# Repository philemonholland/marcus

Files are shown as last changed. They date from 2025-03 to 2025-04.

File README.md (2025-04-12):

# Projet Animatronique : Marcus

Ce dépôt contient le code et la structure d’architecture pour un système d’animatronique capable de détecter des visages, reconnaître des émotions, parler et bouger la tête via des servomoteurs. L’objectif est de permettre à *Marcus* de réagir en temps réel aux personnes qui l’entourent (détection du regard, conversation audio, expressions faciales, etc.).

---

<!-- HTML image Marcus (resized) -->
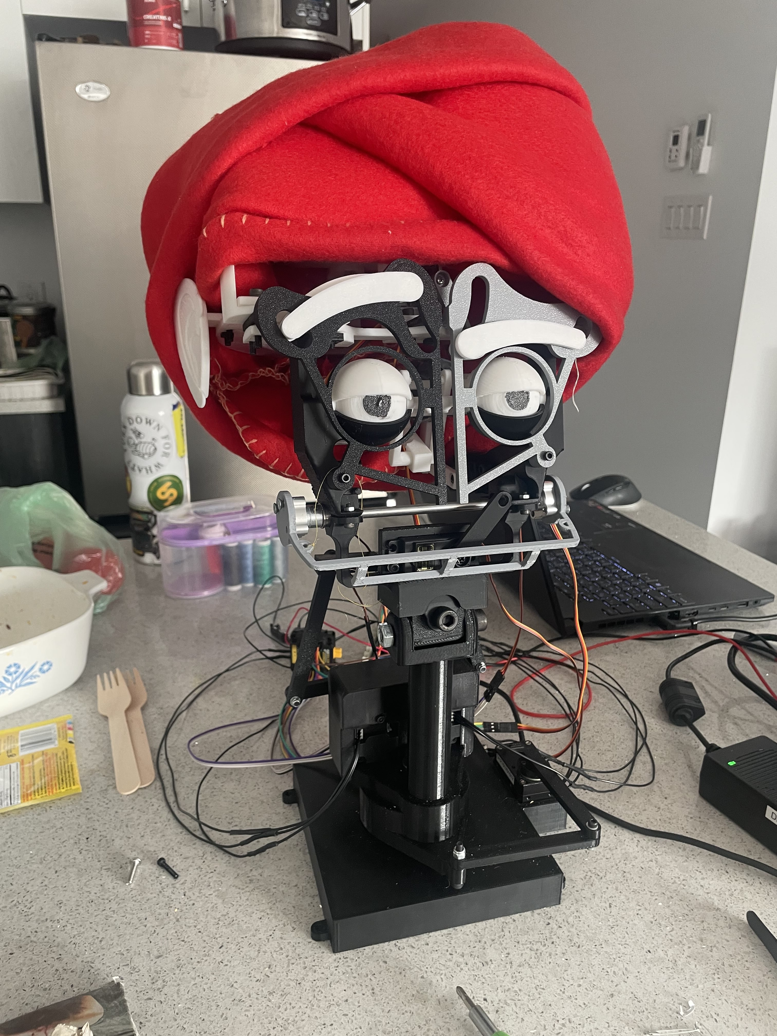
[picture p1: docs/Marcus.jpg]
Marcus illustration


<!-- HTML image Setup (resized) -->
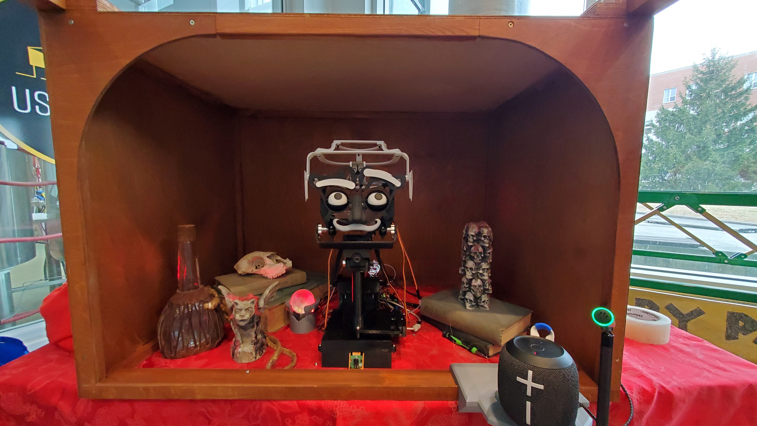
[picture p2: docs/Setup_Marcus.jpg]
Marcus illustration


## Aperçu du fonctionnement

Le diagramme ci-dessous illustre le flux de Communication/Fonctionnement entre les différents composants :

- **Raspberry Pi**  
  *Caméra + Reconnaissance faciale + Reconnaissance d'émotion*  
  Envoi de la position `(x,y,z)` et des émotions détectées via MQTT au PC

- **PC central**  
  - Fait office de **Broker MQTT** 
  - Utilise **Whisper** (STT) pour la reconnaissance vocale  
  - Fait des requêtes au **LLM externe** (OpenAI) via une API REST (avec le contexte : texte + émotion)  
  - Renvoie une réponse texte
  - Gère la **synthèse vocale (TTS)** pour parler via un haut-parleur

- **Arduino OpenRB-150** (contrôle des servos)  
  - Reçoit des commandes UART (*REGARDE, SURPRIS, NON IMPRESSIONER, etc.*)  
  - Envoie son statut (*ready*) au départ  
  - Contrôle effectif des mouvements de la tête

- **Arduino MEGA** (contrôle boule de cristal)  
  - Reçoit des commandes UART (*ALLUME et ÉTEINT*)  
  - Envoie son statut (*ready*) au départ  
  - Contrôle effectif des lumières de la boule de cristal

---

## 📄 License

### Général

Ce projet est distribué sous la licence [MIT](LICENSE) pour tout le code source, les scripts, et les fichiers STL que nous avons créés.  
Veuillez noter que certaines bibliothèques externes utilisées dans ce projet peuvent être soumises à des licences différentes. Il est de votre responsabilité de consulter et de respecter les conditions de licence de ces dépendances.

### 🗣️ Text-to-Speech (TTS)

Ce projet utilise [edge-tts](https://github.com/rany2/edge-tts) pour générer de la parole via le moteur TTS de Microsoft Edge.  
Consultez leur [répertoire GitHub](https://github.com/rany2/edge-tts) pour plus d’informations sur leur licence et leur politique d'utilisation.

### fer2013 : Base de données d'expressions faciales utilisée pour entraîner notre modèle de reconnaissance d'émotion.  
  Source : [Kaggle - FER-2013](https://www.kaggle.com/datasets/msambare/fer2013)  
  Utilisée uniquement à des fins de recherche et d'expérimentation.

### Haar Cascade 
  Utilisé pour la détection de visages. Fichier `haarcascade_frontalface_default.xml` fourni par [OpenCV](https://github.com/opencv/opencv/tree/master/data/haarcascades) sous licence Apache 2.0.

## Structure générale

```bash
marcus/
├── docs/
│   └── ... (Documentation, schémas, etc.)
├── Code/
│   ├── Com/                      (Fonctions de communication MQTT et UART en python)
│   │   └── test_MQTT                             (Code test MQTT entre PC et PI)
│   │   └── test_MQTT_will.py                     (Code test MQTT entre PC et PI avec départ Mosquitto auto)
│   │   └── Test.py                               (Code test pour envoie de commande manuel au OpenRB-150)
│   │   └── dyn_test.py                           (Code test pour envoie de commande manuel spécialisé pour le cou et dynamixel)
│   │   └── Venv_setup.bat                        (Executable pour installer un environnement virtuel avec les requirements automatiquement)
│   │
│   ├── LLM/
│   │   └── marcus_mqtt.py                        (Code principal avec integration complète)
│   │   └── directttsb.py                         (Code modifier pour donner emotion a tts)
│   │   └── whisper_combat.py                     (Code pour transformer les paroles en txt)
│   │   └── Mega.cpp                              (Code pour controler les lumières de la boule de cristal)
│   │
│   ├── Servo/                    (Dossier platformio : Contient le code l'arduino OpenRB-150)
│   │   ├── src/main.cpp                          (Code principal de l'arduino)
│   │   ├── test/Demo.cpp                         (Demo de foncitonnement des moteurs dynamixel)
│   │   └── test/Scan.cpp                         (Code de détection des ID moteurs dynamixel)
│   │   └── test/main_backup.cpp                  (Code main fourni au départ peu modifier)
│   │   └── README                                (Quelque explication du fonctionnement de OpenRB-150)
│   │
│   └── Pi/
│       ├── FaceRecognition.py    (Détection visage, émotion et envoie info MQTT)
│       ├── EmotionRecognitionTraining.py         (Entrainnement d'un modèle IA avec la banque de donné FER2013)
│       ├── fer2013.zip                           (Banque de données FER2013 voir site officiel pour license)
│       ├── haarcascade_frontalface_default.xml   (Modèle IA pour détection de visage voir site officiel pour license)
│       ├── emotion_recognition_model.h5          (Modèle IA entrainé utiliser avec FaceRecognition)
│       ├── 60_model.h5                           (Alternative de modèle IA)
│       └── setup_venv.sh                         (Executable pour installer un environnement virtuel avec les requirements automatiquement)
│
├── STL                           (Dernier fichier stl des pièces imprimer)
│
└── README.md                     (Vous êtes ici)

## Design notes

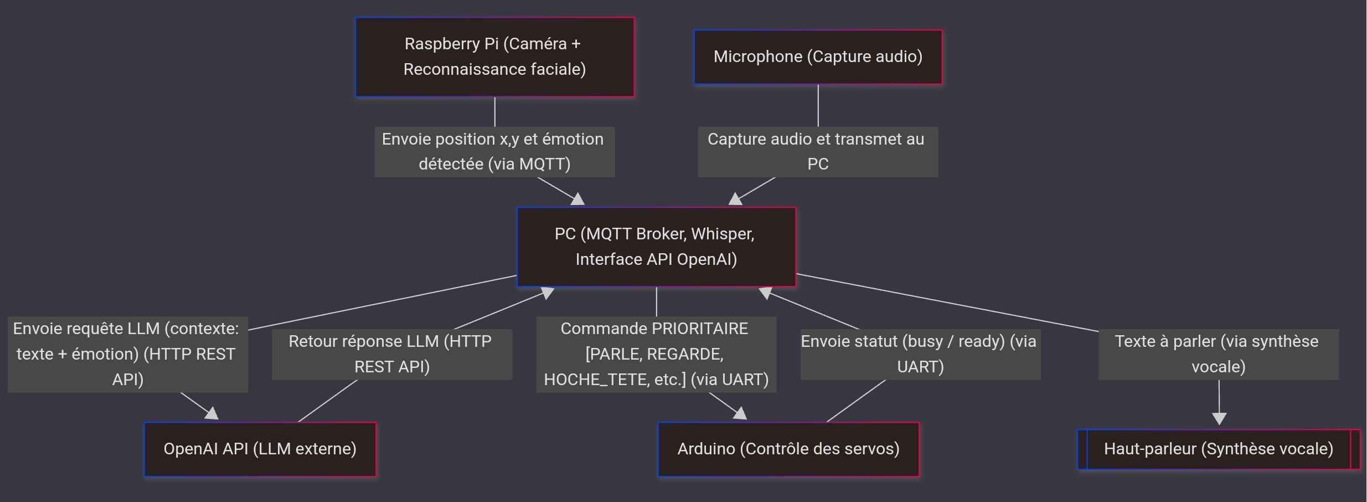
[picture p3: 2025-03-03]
docs/schema_proj.jpg

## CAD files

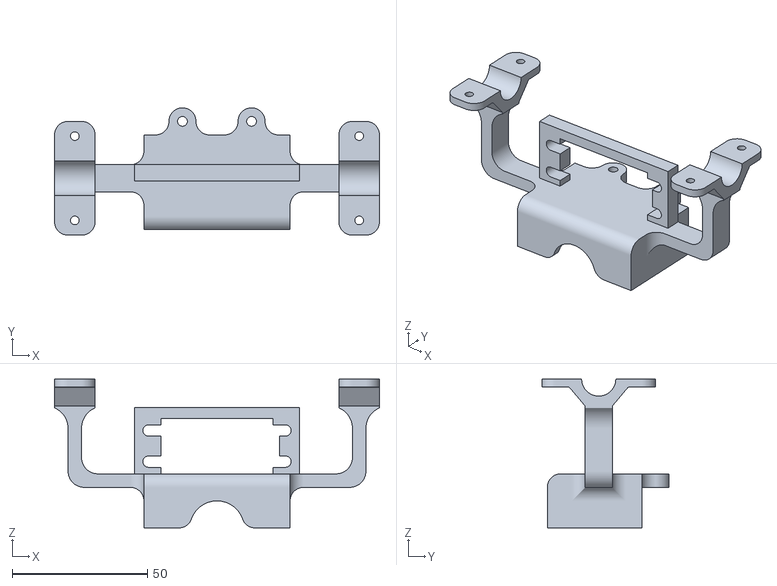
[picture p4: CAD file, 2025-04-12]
STL/Assembly_général/Assembly 1 - Part 1 (26).stl
120.0 x 47.0 x 55.0

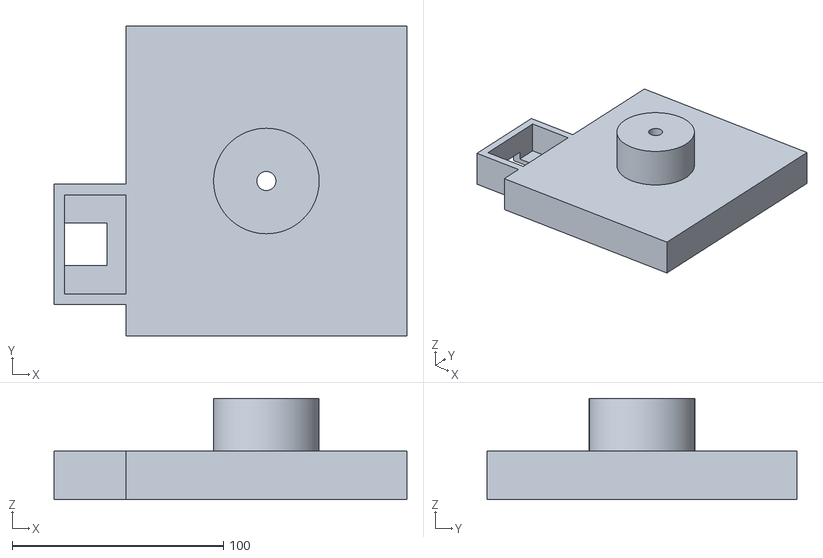
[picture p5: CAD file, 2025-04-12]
STL/Assembly_général/Assembly 1 - Part 1 (28).stl
167.2 x 146.9 x 48.0

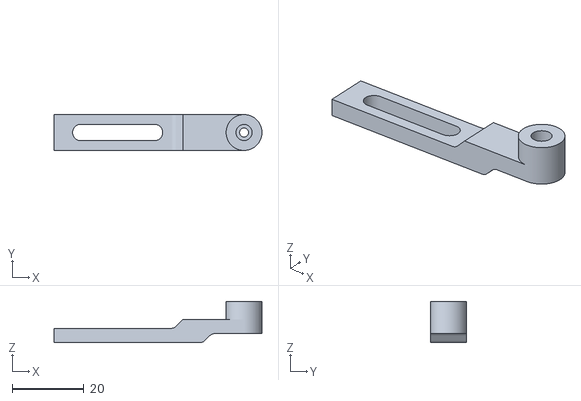
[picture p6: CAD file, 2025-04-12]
STL/Assembly_général/Assembly 1 - Part 1 (12).stl
58.0 x 10.0 x 11.5

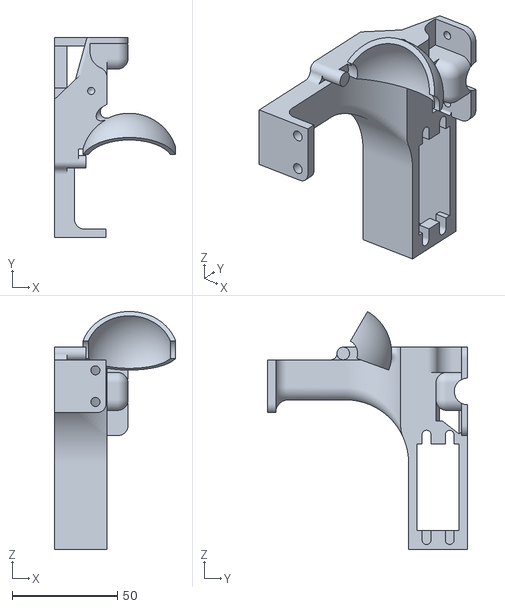
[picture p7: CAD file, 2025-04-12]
STL/Assembly_général/Assembly 1 - Part 1 (18).stl
57.6 x 95.0 x 112.9

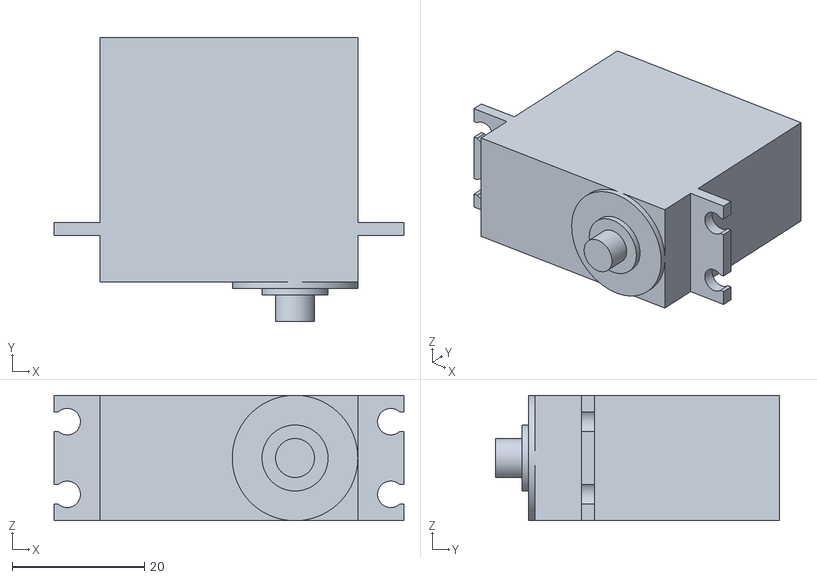
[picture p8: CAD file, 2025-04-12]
STL/Assembly_général/Assembly 1 - Part 1.stl
53.0 x 43.0 x 19.0

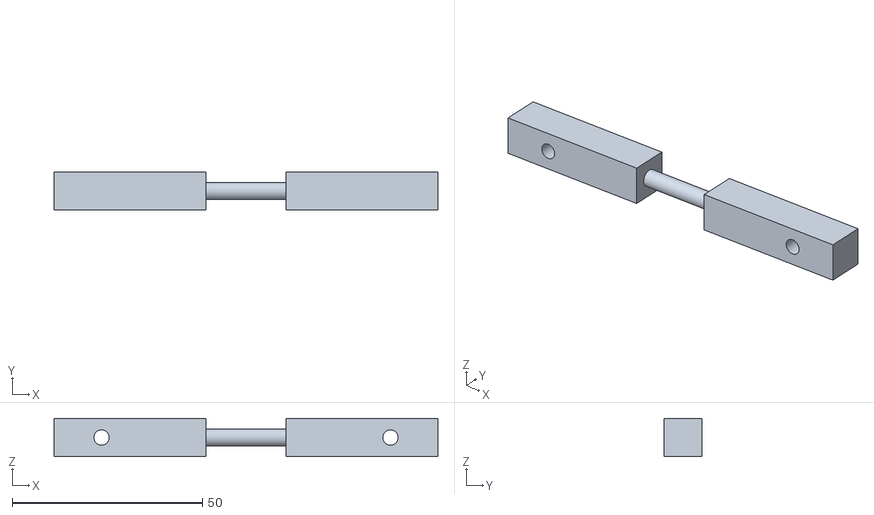
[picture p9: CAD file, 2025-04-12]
STL/Assembly_général/Assembly 1 - Part 4.stl
101.0 x 10.0 x 10.0

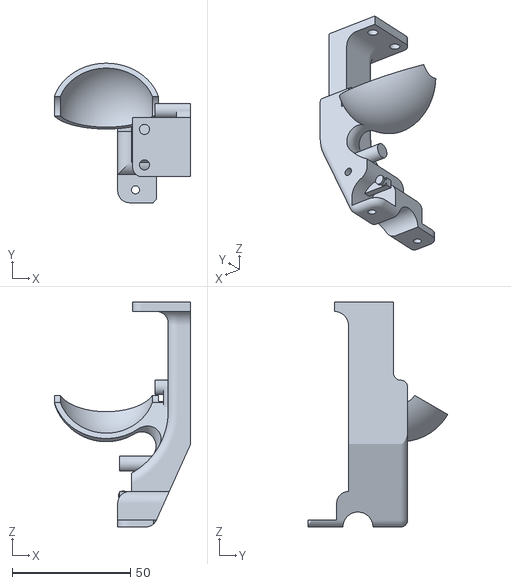
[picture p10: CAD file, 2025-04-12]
STL/Assembly_général/Assembly 1 - Part 1 (19).stl
57.6 x 58.9 x 95.0

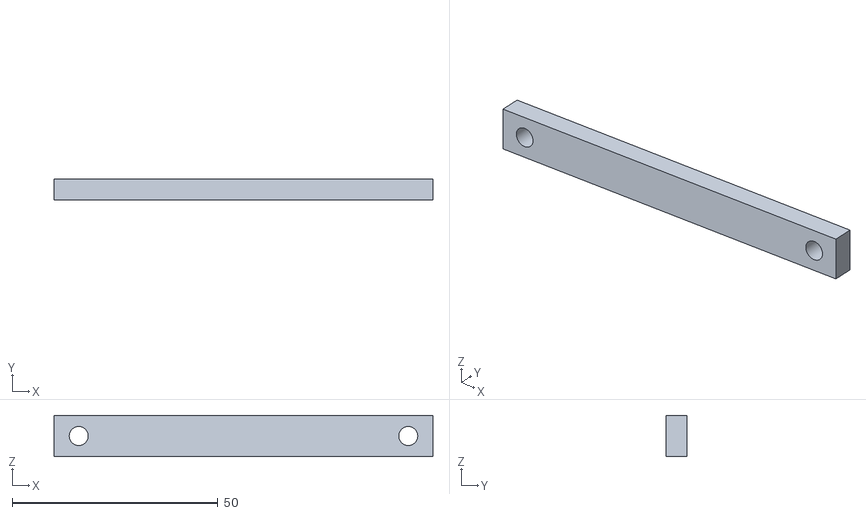
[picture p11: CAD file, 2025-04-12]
STL/Assembly_général/Assembly 1 - Part 1 (11).stl
92.0 x 5.00 x 10.0

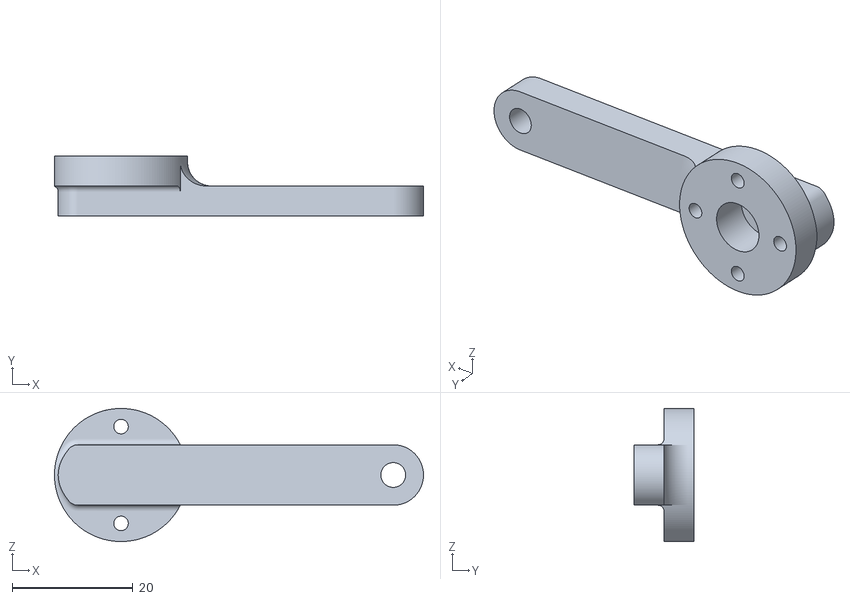
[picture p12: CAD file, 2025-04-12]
STL/Assembly_général/Assembly 1 - Part 1 (10).stl
61.0 x 10.0 x 22.0

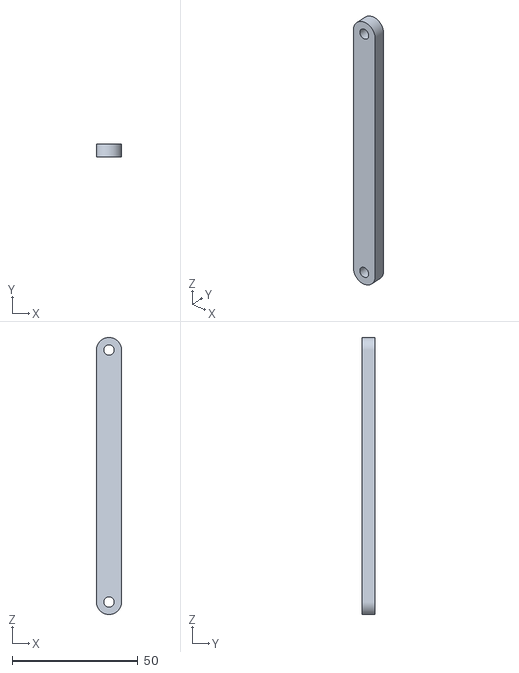
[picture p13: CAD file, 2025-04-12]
STL/Assembly_général/Assembly 1 - Part 2.stl
10.0 x 5.00 x 110.0

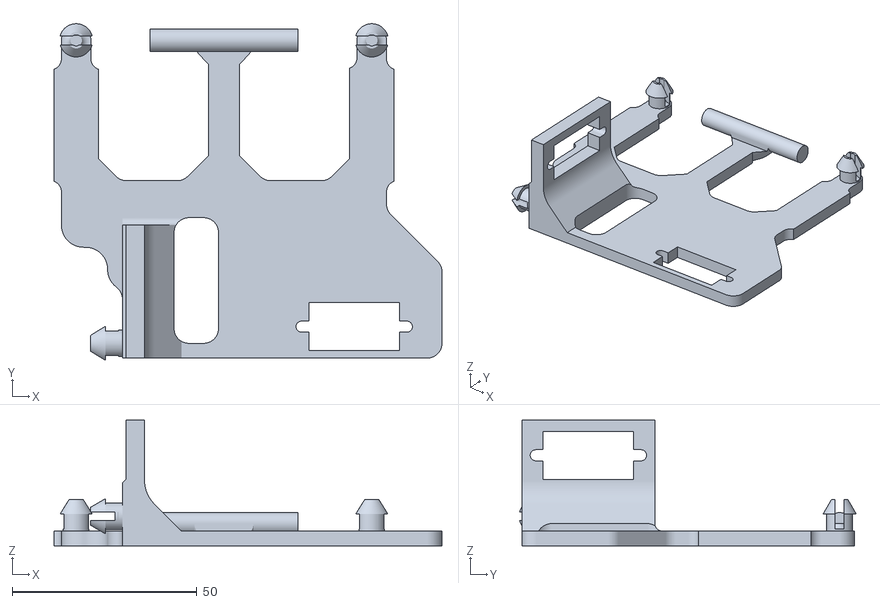
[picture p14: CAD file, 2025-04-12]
STL/Assembly_général/Assembly 1 - Part 1 (17).stl
105.0 x 91.1 x 34.0

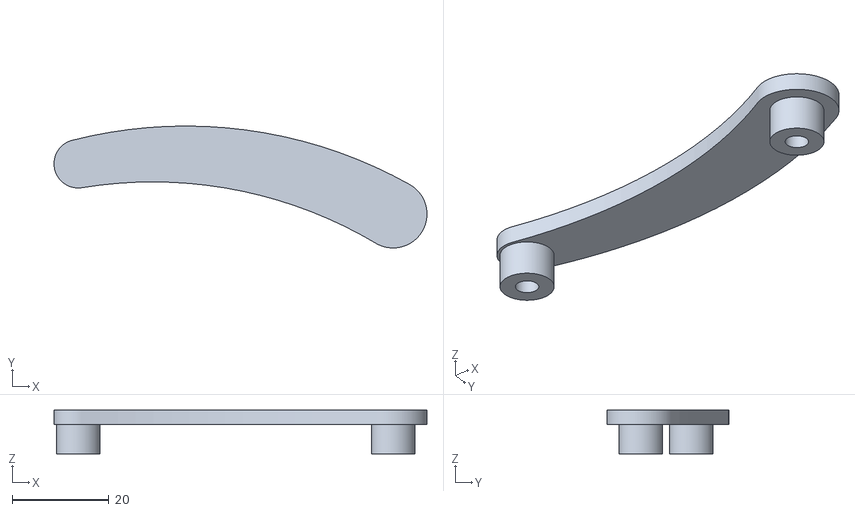
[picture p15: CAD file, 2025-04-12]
STL/Assembly_général/Assembly 1 - Part 1 (22).stl
77.0 x 25.2 x 9.00

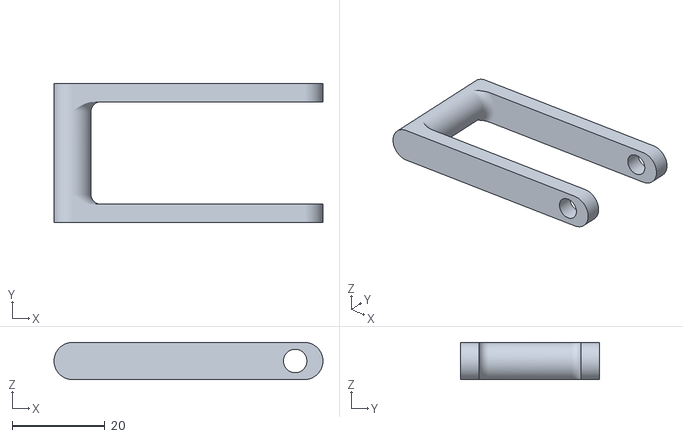
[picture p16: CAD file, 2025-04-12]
STL/Assembly_général/Assembly 1 - Part 1 (16).stl
58.0 x 30.0 x 8.00

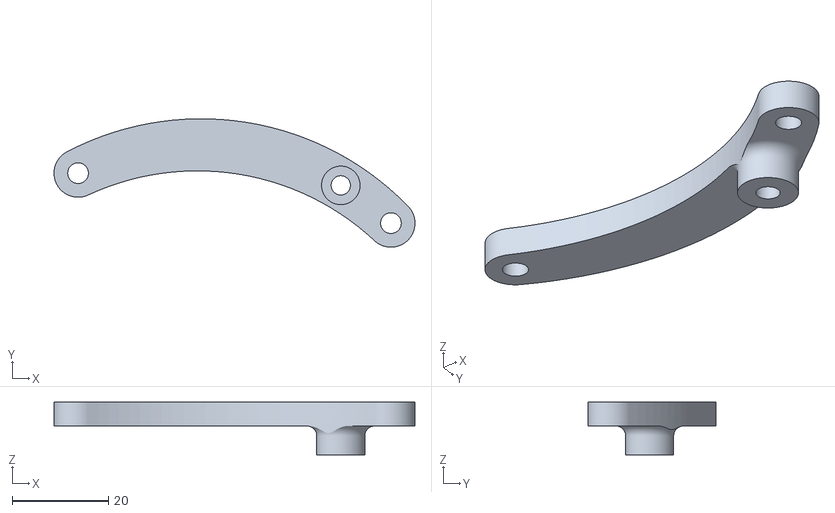
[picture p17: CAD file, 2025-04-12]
STL/Assembly_général/Assembly 1 - Part 1 (25).stl
75.0 x 26.7 x 11.0

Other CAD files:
STL/Assembly_général/Assembly 1 - Part 1 (14).stl
STL/Assembly_général/Assembly 1 - Part 1 (23).stl
STL/Assembly_général/Assembly 1 - Part 1 (20).stl
STL/Assembly_général/Assembly 1 - Part 1 (21).stl
STL/Assembly_général/Assembly 1 - Part 1 (1).stl
STL/Assembly_général/Assembly 1 - Part 1 (13).stl
STL/Assembly_général/Assembly 1 - Part 1 (15).stl
STL/Assembly_général/Assembly 1 - Part 1 (2).stl
STL/Assembly_général/Assembly 1 - Part 1 (24).stl
STL/Assembly_général/Assembly 1 - Part 1 (27).stl
STL/Assembly_général/Assembly 1 - Part 1 (3).stl
STL/Assembly_général/Assembly 1 - Part 1 (4).stl
STL/Assembly_général/Assembly 1 - Part 1 (5).stl
STL/Assembly_général/Assembly 1 - Part 1 (6).stl
STL/Assembly_général/Assembly 1 - Part 1 (7).stl
STL/Assembly_général/Assembly 1 - Part 1 (8).stl
STL/Assembly_général/Assembly 1 - Part 1 (9).stl
STL/Assembly_général/Assembly 1 - Part 2 (1).stl
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

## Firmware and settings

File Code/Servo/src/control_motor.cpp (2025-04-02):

#include <Arduino.h>
#include <Dynamixel2Arduino.h>
#include <Servo.h>
#include <stdio.h>
#include <string.h>

#define PROTOCOL_VERSION 2.0
#define DXL_MIN_ANGLE 0
#define DXL_MAX_ANGLE 4095
#define DXL_MOVING_STATUS_THRESHOLD 20

class Motor {
public:
    virtual void set_angle_degrees(float degrees) = 0;
    virtual int get_angle() = 0;
};

class ServoMotor : public Motor {
public:
    ServoMotor(const char* name, int pin) : name(name), pin(pin), initial_angle(0), angle(0) {
        servo.attach(pin);
        set_angle_degrees(initial_angle);
    }
    void set_angle_degrees(float degrees) override {
        angle = constrain(degrees, 0, 180);
        servo.write(map(angle, 0, 180, 0, 180));
    }
    int get_angle() override {
        return angle;
    }
private:
    const char* name;
    int pin;
    float initial_angle;
    float angle;
    Servo servo;
};

class DynamixelMotor : public Motor {
public:
    DynamixelMotor(const char* name, uint8_t id, uint8_t dir_pin, uint8_t baudrate) 
        : name(name), id(id), initial_angle(2048), angle(2048), driver(Serial1, dir_pin) {
        driver.begin(baudrate);
        set_angle_degrees(initial_angle);
    }
    void set_angle_degrees(float degrees) override {
        int new_angle = map(degrees, 0, 360, DXL_MIN_ANGLE, DXL_MAX_ANGLE);
        set_angle(new_angle);
    }
    int get_angle() override {
        return driver.readControlTableItem(ControlTableItem::PRESENT_POSITION, id);
    }
private:
    void set_angle(int new_angle) {
        angle = constrain(new_angle, DXL_MIN_ANGLE, DXL_MAX_ANGLE);
        driver.writeControlTableItem(ControlTableItem::GOAL_POSITION, id, angle);
    }
    const char* name;
    uint8_t id;
    int initial_angle;
    int angle;
    Dynamixel2Arduino driver;
};

class MotorController {
public:
    void add_motor(Motor* motor, const char* name) {
        if (motor_count < MAX_MOTORS) {
            motors[motor_count].motor = motor;
            motors[motor_count].name = name;
            motor_count++;
        }
    }

    void set_motor(const char* name, float degrees) {
        Motor* motor = find_motor(name);
        if (motor) {
            motor->set_angle_degrees(degrees);
        }
    }

    int get_motor(const char* name) {
        Motor* motor = find_motor(name);
        return motor ? motor->get_angle() : -1;
    }
    
    void reset_all() {
        for (int i = 0; i < motor_count; i++) {
            motors[i].motor->set_angle_degrees(0);
        }
    }

    void set_mirrored_motors(const char* motor1_name, const char* motor2_name, float degrees) {
        Motor* motor1 = find_motor(motor1_name);
        Motor* motor2 = find_motor(motor2_name);
        
        if (motor1 && motor2) {
            float angles = compute_motor_angles(degrees);
            motor1->set_angle_degrees(angles);
            motor2->set_angle_degrees(180 - angles);
        }
    }

    float compute_motor_angle(float pourcentage, const std::string& side = "right") {

        float angle_min = 95.669;
        float angle_max = 151.228931;
        
        float angle_moteur = map(pourcentage, 0, 100, angle_min, angle_max);
    
        if (side == "left") {
            angle_moteur = angle_max - (angle_moteur - angle_min);
        }
    
        return angle_moteur;
    }
    

    void base_motor(const char* motor_name, float degrees) {
        Motor* motor = find_motor(motor_name);
        
        if (motor) {
            float angles = map(degrees, 45, 135, 45, 135);  // changer les valeurs de 45 et 135 pour avoir les angles limites du moteur et leur proportionalité de mouvement tête
            motor->set_angle_degrees(angles);
        }
    }

    float* compute_motor_angles(float final_angle) {

        float norm_value = map(final_angle, 60, 135, 0, 1);  // changer les valeurs de 60 et 135 pour avoir l'angle le plus bas de la tête et l'angle le plus haut
    
        float motor_angle = map(norm_value, 0, 1, 25, 180); // changer les valeurs de 25 et 180 pour avoir l'angle limite des moteurs
    
        float angles = motor_angle;
    
        return angles;
    }


private:
    static constexpr int MAX_MOTORS = 10;
    struct MotorEntry {
        const char* name;
        Motor* motor;
    } motors[MAX_MOTORS];
    int motor_count = 0;
    
    Motor* find_motor(const char* name) {
        for (int i = 0; i < motor_count; i++) {
            if (strcmp(motors[i].name, name) == 0) {
                return motors[i].motor;
            }
        }
        return nullptr;
    }
};

ServoMotor xServo("xServo", 2);
ServoMotor yServo("yServo", 3);
DynamixelMotor xDyn("xDyn", 1, 2, 57600);
DynamixelMotor yDyn("yDyn", 2, 2, 57600);
MotorController controller;

void setup() {
    controller.add_motor(&xServo, "xServo");
    controller.add_motor(&yServo, "yServo");
    controller.add_motor(&xDyn, "xDyn");
    controller.add_motor(&yDyn, "yDyn");
}

void loop() {
    if(controller.get_motor("xServo") == 0 && controller.get_motor("yServo") == 0) {
        controller.set_motor("xServo", 180);
        controller.set_motor("yServo", 180);
    } 
    else if(controller.get_motor("xServo") == 180 && controller.get_motor("yServo") == 180) {
        controller.set_motor("xServo", 0);
        controller.set_motor("yServo", 0);
    }
}

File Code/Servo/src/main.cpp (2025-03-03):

#include <Dynamixel2Arduino.h>
#include <Servo.h>



// Setup environnement dynamixel

#if defined(ARDUINO_OpenRB)  
  #define DXL_SERIAL Serial1 // OpenRB-150 uses Serial1 for Dynamixel
  #define PC_SERIAL Serial // USB Serial for PC communication

  const int DXL_DIR_PIN = -1;
  const float DXL_PROTOCOL_VERSION = 2.0;

  Dynamixel2Arduino dxl(DXL_SERIAL);
#else
  break; // Erreur pas la bonne carte
#endif




// Definition des ID moteurs dynamixel

int DXL_IDs[] = 
{

  3, // ID du moteur droit (To verify)
  4, // ID du moteur gauche (To verify)
  20 // ID du moteur rotation bas

}; // Peuvent etre brancher sur n'importe quel port dynamixel

const int N_DXL = sizeof(DXL_IDs) / sizeof(DXL_IDs[0]);




// Definition des ports des servo PWM


Servo Servos_PWM[6]
{
    Servo(), // Servo 0
    Servo(), // Servo 1
    Servo(), // Servo 2
    Servo(), // Servo 3
    Servo(), // Servo 4
    Servo()  // Servo 5
};





// Definition des commandes recu

struct Command {
    int mode;
    int value;
    int id;
};

Command receivedData;
bool commandReceived = false;




void setup() {

    PC_SERIAL.begin(115200);  // USB Serial for PC communication

    while (!PC_SERIAL);       // Wait for serial connection
    PC_SERIAL.println("Starting Setup...");


    // Set Port baudrate to 57600bps. This has to match with DYNAMIXEL baudrate.
    dxl.begin(57600);
    if (dxl.getLastLibErrCode()) {
        PC_SERIAL.println("Could not init serial port!");
        PC_SERIAL.print("Last error code: ");
        PC_SERIAL.println(dxl.getLastLibErrCode());
    }
    // Set Port Protocol Version. This has to match with DYNAMIXEL protocol version.
    if (!dxl.setPortProtocolVersion(DXL_PROTOCOL_VERSION)) {
        PC_SERIAL.println("Could not set protocol version!");
        PC_SERIAL.print("Last error code: ");
        PC_SERIAL.println(dxl.getLastLibErrCode());
    }

    PC_SERIAL.println("Configuring Dynamixel motors...");
    for (int i = 0; i < N_DXL; i++) {

        uint8_t id = DXL_IDs[i];

        if (dxl.ping(id)) {
            dxl.torqueOff(id);
            dxl.setOperatingMode(id, OP_POSITION);
            dxl.torqueOn(id);

            // Limit the maximum velocity in Position Control Mode. Use 0 for Max speed
            dxl.writeControlTableItem(ControlTableItem::PROFILE_VELOCITY, id, 30);

            PC_SERIAL.print("✅ Moteur ID ");
            PC_SERIAL.print(id);
            PC_SERIAL.println(" initialisé !");
        }

        else {
            PC_SERIAL.print("❌ Échec du ping du moteur ID ");
            PC_SERIAL.println(id);
        }
    }

    PC_SERIAL.println("Configuring PWM servos...");

    for (uint8_t i = 0; i < 6; i++) {

        Servos_PWM[i].attach(i);
        PC_SERIAL.print("✅ Moteur ID ");
        PC_SERIAL.print(i);
        PC_SERIAL.println(" initialisé !");
    }
    
    
    PC_SERIAL.println("READY");  // Signale au PC que l'Arduino est prêt

}




void loop() {
    if (Serial.available()) {
        String input = Serial.readStringUntil('\n'); // Lire jusqu'au saut de ligne
        if (sscanf(input.c_str(), "%d,%d,%d", &receivedData.mode, &receivedData.value, &receivedData.id) == 3) {
            commandReceived = true;
        }
    }

    if (commandReceived) {
        //Serial.print("Mode: "); Serial.print(receivedData.mode);
        //Serial.print(" | Value: "); Serial.print(receivedData.value);
        //Serial.print(" | ID: "); Serial.println(receivedData.id);


        switch (receivedData.mode)
        {
        case 0: // Set position dynamixel
            Serial.println("Setting position dynamixel...");
            dxl.setGoalPosition(receivedData.id, receivedData.value, UNIT_DEGREE);
            break;

        case 1: // Set position PWM
            Serial.println("Setting position PWM...");
            Servos_PWM[receivedData.id].write(receivedData.value);
            break;
        
        default:
        Serial.println("❌ Commande non reconnue !");
            break;
        }

        commandReceived = false;
        
    }

    //PC_SERIAL.println("READY");  // Signale au PC que l'Arduino est prêt

    
    //delay(5);
}

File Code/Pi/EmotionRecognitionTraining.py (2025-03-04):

import tensorflow as tf
from tensorflow.keras import layers, models
from tensorflow.keras.optimizers import Adam
from tensorflow.keras.optimizers.schedules import ExponentialDecay
from tensorflow.keras.preprocessing.image import ImageDataGenerator
import cv2
import numpy as np
from tensorflow.keras.models import load_model


# Check if GPU is available
gpus = tf.config.experimental.list_physical_devices('GPU')
if gpus:
    try:
        # Set memory growth to avoid TensorFlow reserving all GPU memory
        for gpu in gpus:
            tf.config.experimental.set_memory_growth(gpu, True)
        print(f"Using GPU: {gpus}")
    except RuntimeError as e:
        print(e)
else:
    print("GPU not found. Running on CPU.")

# Define paths
data_dir = ".\\fer2013"

# Dataset configuration
batch_size = 64*2
img_height = 48
img_width = 48

# Data augmentation using ImageDataGenerator
train_datagen = ImageDataGenerator(
    rescale=1.0 / 255,
    rotation_range=30,
    width_shift_range=0.2,
    height_shift_range=0.2,
    zoom_range=0.2,
    horizontal_flip=True,
    fill_mode='nearest',
    validation_split=0.2
)

val_datagen = ImageDataGenerator(rescale=1.0 / 255, validation_split=0.2)

# Apply the image generators
train_generator = train_datagen.flow_from_directory(
    data_dir,
    subset="training",
    seed=123,
    batch_size=batch_size,
    color_mode="grayscale",
    target_size=(img_height, img_width),
    class_mode='sparse'
)

val_generator = val_datagen.flow_from_directory(
    data_dir,
    subset="validation",
    seed=123,
    batch_size=batch_size,
    color_mode="grayscale",
    target_size=(img_height, img_width),
    class_mode='sparse'
)

# Model architecture with Batch Normalization
model = models.Sequential([
    layers.Conv2D(64, (3, 3), activation='relu', input_shape=(48, 48, 1)),
    layers.BatchNormalization(),
    layers.Conv2D(64, (3, 3), activation='relu'),
    layers.BatchNormalization(),
    layers.MaxPooling2D((2, 2)),
    
    layers.Conv2D(128, (3, 3), activation='relu'),
    layers.BatchNormalization(),
    layers.Conv2D(128, (3, 3), activation='relu'),
    layers.BatchNormalization(),
    layers.MaxPooling2D((2, 2)),
    
    layers.Conv2D(256, (3, 3), activation='relu'),
    layers.BatchNormalization(),
    layers.MaxPooling2D((2, 2)),

    layers.Flatten(),
    layers.Dense(256, activation='relu'),
    layers.Dropout(0.5),
    layers.BatchNormalization(),
    layers.Dense(7, activation='softmax')
])

# Define a learning rate schedule
lr_schedule = ExponentialDecay(
    initial_learning_rate=0.001, # Lower to avoid overshooting
    decay_steps=5000,            # Slow decay
    decay_rate=0.95               # Slower decay for more fine-tuning
)



# Compile the model
optimizer = Adam(learning_rate=lr_schedule)
model.compile(optimizer=optimizer,
              loss='sparse_categorical_crossentropy',
              metrics=['accuracy'])

model.summary()

# Train the model with the data generator
history = model.fit(
    train_generator,
    validation_data=val_generator,
    epochs=50
)

# Save the model
model.save('emotion_recognition_model.h5')

# Evaluate the model on the validation set
test_loss, test_accuracy = model.evaluate(val_generator)
print(f"Validation accuracy: {test_accuracy:.2f}")


cap.release()
cv2.destroyAllWindows()

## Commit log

2025-03-01 Debut de communication
    Code python test.py communique avec le mains. Pour le moment seulement un mode manuel existe
2025-03-03 Fix Unit
    Unité mise en degrée + délai enlever
    [main.cpp]
2025-03-03 Changement de nom de fichier
    [arduino_zero.cfg]
2025-03-04 Add files via upload
    Ce code permet de tester la communication MQTT entre PC et le raspberry PI. Pour que ça fonctionne, vous devez absolument installer un broker Mosquitto MQTT sur votre ordinateur (ça se download facilement en ligne) . Ensuite, il faut désactiver une règle dans le firewall de votre PC et l'activer, sinon le Pi ne sera pas capable de lui envoyer des messages. Voici la règle à activer : Partage de fichiers et d'imprimantes (Demande d'écho -- ICMPv4 Entrant)
    [test_MQTT.py]
2025-03-29 Add files via upload
    - J'ai intégré le code de communication UART avec le code de l'IA
    - Multi-threading en asynchrone
    - Allume une lumière lorsque Marcus analyse une réponse, et la ferme lorsqu'il a terminé de parlé
    - ****** Il faut tester avec le PI qui va communiquer par MQTT et rajouter l'envoi des commandes à l'arduino en plus
2025-03-29 Add files via upload
    - Code qui roule sur l'arduino mega pour faire allumer ou fermer une lumière lorsque Marcus analyse les signaux neuroquantiques
2025-04-02 control motor
2025-04-02 Add files via upload
    Fonctionnel avec MQTT (enfin)
    - Reste à implémenter le passage propre des valeurs d'angles au Arduino des moteurs
    ***********faut absolument exécuter le code du pi APRES L'EXÉCUTION du code sur l'ordi, sinon le pi envoie rien
